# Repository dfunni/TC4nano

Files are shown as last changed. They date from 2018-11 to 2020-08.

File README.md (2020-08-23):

# TC4nano
The TC4nano is an Arduino Nano shield for termperature logging (up to 4 thermocouples) and PID control of a resistive heating element for use in home coffee roasting (based off of the TC4 Arduino Uno shield design copyright 2014 MLG Properties LLC and bvwelch.com CC-BY). The TC4nano includes one onboard SSR for heater control via slow PWM. Forced air is recommended for cooling the SSR in configurations drawing 10A or above.

### CONTENTS:
1. Configuring Artiasn
2. Updating TC4 Firmware
3. Troubleshooting

The TC4nano is pre-configured for the Artisan roaster-scope software using the aArtisanQ_PID_6_2_3 by Jim Gallt and Brad
Collins provided under BSD Liscense.

TC4 firmware can be found at:
https://github.com/greencardigan/TC4-shield

Artisan can be found at:	
https://github.com/artisan-roaster-scope

Artisan installation instructions:
https://github.com/artisan-roaster-scope/artisan/blob/master/wiki/Installation.md

## 1. CONFIGURING ARTISAN

### General Config
The configuration below assumes use with Poppery I roaster and no fan control through Artisan. 

For Poppery II or other DC fan systems, fan control can be added by connecting a DC motor driver to the IO3 jumper. For AC fan control, zero cross detection circuitry and an additional random fire SSR are required as well as reflashing the Arduino firmware with different configuration settings. For Artisan configuration with fan control see the setup described here: https://www.youtube.com/watch?v=0-Co-pXF2NM. 

#### Config > Device...

ET/BT tab:
- select TC4 radio button
- ET Channel - 2
- BT Channel - 1
- AT Channel - None
- PID Firmware - unchecked
- Control - checked
- Curves: ET - unchecked BT - checked
- LCDs: ET - unchecked BT - checked Swap - unchecked

Extra Devices tab:
- Add two devices

Device 1: 
- Device - ArduinoTC4 56 
- Label1 - "Heater" 

Device 2:
- Device - ArduinoTC4 78
- Label1 - "SV" 
- Label2 - "AT"

Note: after clicking "OK" in the Device menu the Port menu will automatically pop up. Prior to each roast session ensure the port reflects the correct Arduino.

#### Config > Sampling Interval 
- set to "1.0" seconds

#### Config > Curves... > RoR tab
- check the boxes for curves and LCDs you want to view and check projection

#### Config > Events

Config tab:
- Annotations - check
- 1 - uncheck - Fan
- 2 - check - Heater
- 3 - uncheck - Damper
- 4 - uncheck - Burner
- Auto CHARGE/Auto Drop/Mark MET/Show Time Guide - uncheck

Buttons tab:
- add one button
- Label - "Heater Off"
- Type - Heater
- Value - 0
- Action - Serial Command
- Documentation - "OT1;0"
- Visibility - ON

Sliders tab:
- In the heater row set the following to:
- Heater - check
- Action - Serial Command
- Command - "OT1;{}"
- Offset - 0.0
- Factor - 1
- Min - 0
- Max - 100
- Fan - uncheck
- Damper - uncheck
- Burner - uncheck

#### Config > Temperature
- Select Fahrenheit or Celcius mode

### PID Config

Click the blue CONTROL button (ensure Control is checked under Config > Device)

Recommended starting PID parameters:

| | kp  | ki | kd  |
|---|-----|---|-----|
| Poppery I  | 2.2 | 0.08 | 20  |
| Poppery II | 1.3 | 0.06 | 4.5 |

- Source - BT

Target:
- Positive - Heater
- Negative - None

Set Value:
- Mode - Background (ensure background profile is loaded prior to roasting)
- Lookahead - 10s (adjust as necessary)

- Start PID on CHARGE - check

### Creating a Profile

#### Tools > Designer

Adjust the circles to the desired locations, add or delete points as necessary.

When profile is complete go to Tools > Designer (uncheck) and proile will be
loaded onto the graph.

Hit the RESET button, then save the profile to your Profiles directory.

### Loading a Background Profile

#### Roast > Background

- Show - check
- BT - check
- All others - uncheck
- Align - CHARGE
- Load - select a saved profile from your profile directory

## 2. UPDATING TC4 FIRMWARE

The latest version of the TC4 firmware can be found on github. Version 
6.6 zip file can be found at:
https://github.com/greencardigan/TC4-shield/tree/master/applications/Artisan/aArtisan_PID/tags/REL_aArtisanQ_PID_6_6

Once downloaded open aArtisanQ_PID.ino in the Arduino IDE 
(https://www.arduino.cc). This will open all of the other files from the
aArtisanQ_PID folder as seperate tabs in the IDE.

Select the user.h tab and to choose the options you wish to enable by 
uncommenting/commenting the options in this file.

- Under "Base configuration" ensure CONFIG_PWM is selected as the 
TC4nano does not include a ZCD.

- Under "Tempreature Unit" comment out CELCIUS if Fahrenhiet is desired.

When all appropriate changes are made, connect the Arduino to the computer and
select the following settings from the menu bar:

- Tools > Board > Arduino Nano
- Tools > Processor > ATMega328P (Old Bootloader)
- Tools > Port > /dev/cu.YOUR_ARDUINO

Finally, flash the Adduino Nano by clicking the upload (forward arrow) button 
in the Arduino IDE. A display of the progress will appear in the command prompt
at the bottom of the IDE and "Done Uploading" will display when it completes 
sucessfully.

## 3. TROUBLESHOOTING:

### Generic Arduino Not Recognized (macOS)

Copy and paste these commands into terminal one by one 
(to open terminal press command+space and type 'terminal', then hit enter):

First check to see if homebrew is installed

    brew --version

If it is not installed (ie you get an output that is something other than
the version of homebrew) run the following commmand

    /usr/bin/ruby -e "$(curl -fsSL https://raw.githubusercontent.com/Homebrew/install/master/install)"

Then run the following two commands to install the CH34x drivers needed
to use the generic arduino nano

    brew tap mengbo/ch340g-ch34g-ch34x-mac-os-x-driver https://github.com/mengbo/ch340g-ch34g-ch34x-mac-os-x-driver
    brew cask install wch-ch34x-usb-serial-driver

Now restart your computer, and see if Artisan recognizes the arduino.
Alternately, you can enter the following in the terminal and look for an output
that is not an error.

    ls /dev/cu.usb* /dev/cu.wch*

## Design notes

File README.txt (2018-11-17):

# TC4nano
The configuration specified in this document is for the TC4nano which uses
one SSR for heater control (no fan control) and logs BT only.

CONTENTS:
Configuring Artiasn
- General Config
- PID Config
- Creating a Profile
- Loading a Background Profile
Updating TC4 Firmware
Troubleshooting
- Generic Arduino Nano Not Recognized

The TC4nano is configured for the Artisan roaster-scope software. The latest 
version can be found at:	
https://artisan-roasterscope.blogspot.com

Artisan installation instructions:
https://github.com/artisan-roaster-scope/artisan/blob/master/wiki/Installation.md

The TC4nano comes preloaded with aArtisanQ_PID_6_2_3 by Jim Gallt and Brad
Collins and is provided under BSD Liscense. 

The provided firmware has been tested with Artisan versions up to 1.5. 
If you wish to update the firmware the instructions are provided below.

*******************************************************************************

CONFIGURING ARTISAN

Leave defaults unless specified below. Text input is listed in " ".

===============================================================================
General Config
---------------------------------
Config > Device...

> ET/BT tab:
select TC4 radio button
ET Channel - 1
BT Channel - 2
AT Channel - None
PID Firmware - unchecked
Control - checked
Curves: ET - unchecked BT - checked
LCDs: ET - unchecked BT - checked Swap - unchecked

> Extra Devices tab:
Add two devices

Device 1: 
Device - ArduinoTC4 56 
Label1 - "Heater" 
Label2 - "Fan"

Device 2:
Device - ArduinoTC4 78
Label1 - "SV" 
Label2 - "AT"
OK

Note: after clicking "OK" in the Device menu the Port menu will automatically
pop up. Leave this as default for now. When roasting ensure the port reflects
the TC4's Arduino.
OK
---------------------------------

Config > Sampling Interval 
set to "1.0" seconds
OK
---------------------------------

Config > Curves... > RoR tab
check the boxes for curves and LCDs you want to view and check projection
OK
---------------------------------

Config > Events

> Config tab:
Annotations - check
1 - check - "Fan"
2 - check - "Heater"
3 - uncheck
4 - uncheck
Auto CHARGE/Auto Drop/Mark MET/Show Time Guide - uncheck

> Buttons tab
add one button
Label - "Fan Off"
Type - Fan
Value - 0
Action - Serial Command
Documentation - "IO3;0"
Visibility - ON

> Sliders tab
In the heater row set the following to:
Heater - check
Action - Serial Command
Command - "OT1;{}"
Offset - 0.0
Factor - 1
Min - 0
Max - 100

Fan - uncheck
Damper - uncheck
Burner - uncheck
OK
---------------------------------
Config > Temperature
Select Fahrenheit or Celcius mode
OK
---------------------------------

===============================================================================
PID Config

Click the blue CONTROL button (ensure Control is checked under Config > Device)

For Poppery I a good starting point is:
kp = 2.2; ki = 0.08; kd = 20

For Poppery II start with:
kp = 1.3; ki = 0.06; kd = 4.5

Source - BT

Target:
Positive - Heater
Negative - None

Set Value:
Mode - Background (ensure background profile is loaded prior to roasting)
Lookahead - 10s (adjust as necessary)

Start PID on CHARGE - check
OK

===============================================================================
Creating a Profile

Tools > Designer

Adjust the circles to the desired locations, add or delete points as necessary.

When profile is coplete go to Tools > Designer (uncheck) and proile will be
loaded onto the graph.

Hit the RESET button, then save the profile to your Profiles directory.

===============================================================================
Loading a Background Profile

Roast > Background

Show - check
BT - check
All others - uncheck
Align - CHARGE
Load - select a saved profile from your profile directory
OK

*******************************************************************************

UPDATING TC4 FIRMWARE

The latest version of the TC4 firmware can be found on github. Version 
6.6 zip file can be found at:
https://github.com/greencardigan/TC4-shield/tree/master/applications/Artisan/aArtisan_PID/tags/REL_aArtisanQ_PID_6_6

Once downloaded open aArtisanQ_PID.ino in the Arduino IDE 
(https://www.arduino.cc). This will open all of the other files from the
aArtisanQ_PID folder as seperate tabs in the IDE.

Select the user.h tab and to choose the options you wish to enable by 
uncommenting/commenting the options in this file.

- Under "Base configuration" ensure CONFIG_PWM is selected since the 
TC4nano does not include a ZCD.

- Under "Tempreature Unit" comment out CELCIUS if Fahrenhiet is desired.

- Leave all 4 "TC_TYPEx typeK" enabled under "Thermocouple Input Options"
even though only one thermocouple will be used.

- Ensure Baud rate of BAUD 115200

When all appropriate changes are made, connect the arduino to the computer and
select the following options from the menu bar:

Tools > Board > Arduino Nano
Tools > Processor > ATMega328P (Old Bootloader)
Tools > Port > /dev/cu.YOUR_ARDUINO

Finally, flash the Adduino Nano by clicking the upload (forward arrow) button 
in the Arduino IDE. A display of the progress will appear in the command prompt
at the bottom of the IDE and "Done Uploading" will display when it completes 
sucessfully.

*******************************************************************************

TROUBLESHOOTING:

===============================================================================
Generic Arduino Not Recognized

Copy and paste these commands into terminal one by one 
(to open terminal press command+space and type terminal, then hit enter):

First check to see if homebrew is installed

_______________________________________________________________________________
brew -v
_______________________________________________________________________________

If it is not installed (ie you get an output that is something other than
the version of homebrew) run the following commmand... this takes a while

_______________________________________________________________________________
/usr/bin/ruby -e "$(curl -fsSL https://raw.githubusercontent.com/Homebrew/install/master/install)"
_______________________________________________________________________________

Then run the following two commands to install the CH34x drivers needed
to use the generic arduino nano

_______________________________________________________________________________
brew tap mengbo/ch340g-ch34g-ch34x-mac-os-x-driver https://github.com/mengbo/ch340g-ch34g-ch34x-mac-os-x-driver
_______________________________________________________________________________

_______________________________________________________________________________
brew cask install wch-ch34x-usb-serial-driver
_______________________________________________________________________________

Now restart your computer, and see if Artisan recognizes the arduino.
Or you can enter the following in the terminal and look for an output
that is not an error.

_______________________________________________________________________________
ls /dev/cu.usb* /dev/cu.wch*
_______________________________________________________________________________

===============================================================================

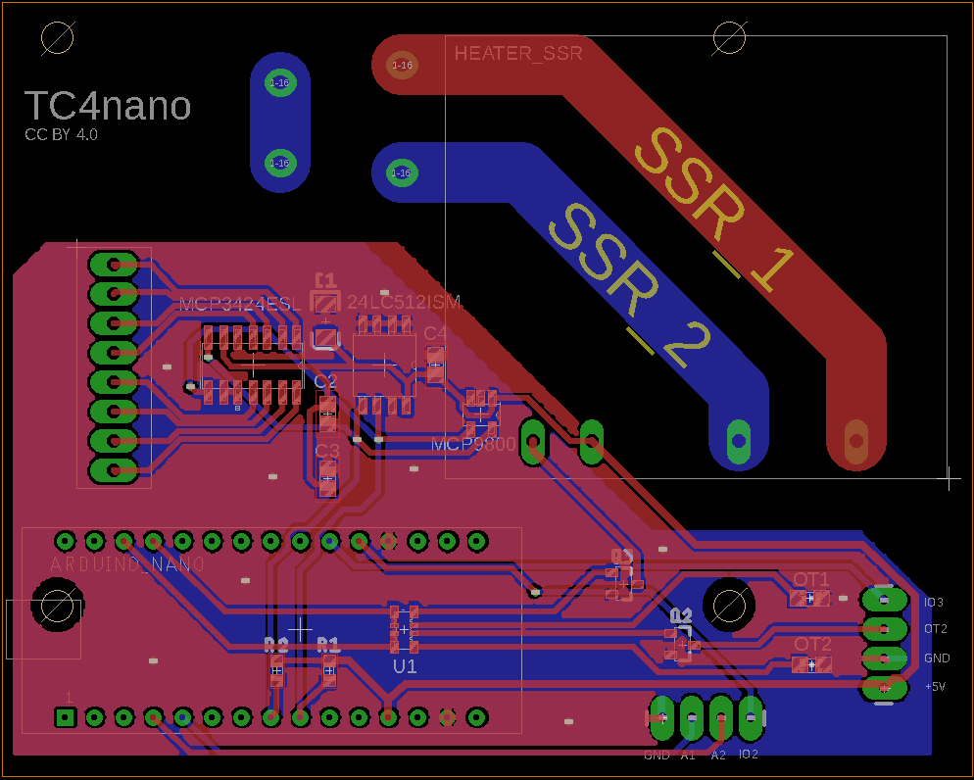
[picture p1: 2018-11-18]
Hardware/TC4nano_v2_brd.png

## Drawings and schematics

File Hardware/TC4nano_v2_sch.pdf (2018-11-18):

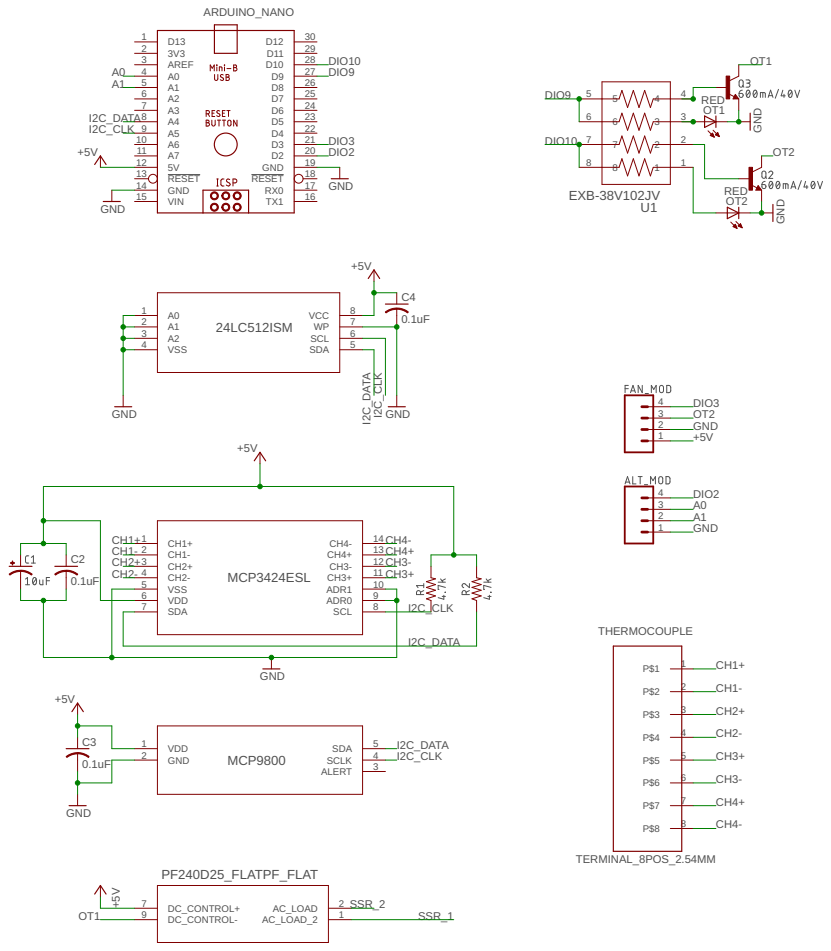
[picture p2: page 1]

2 | 7 VCC
3 | 6 WP

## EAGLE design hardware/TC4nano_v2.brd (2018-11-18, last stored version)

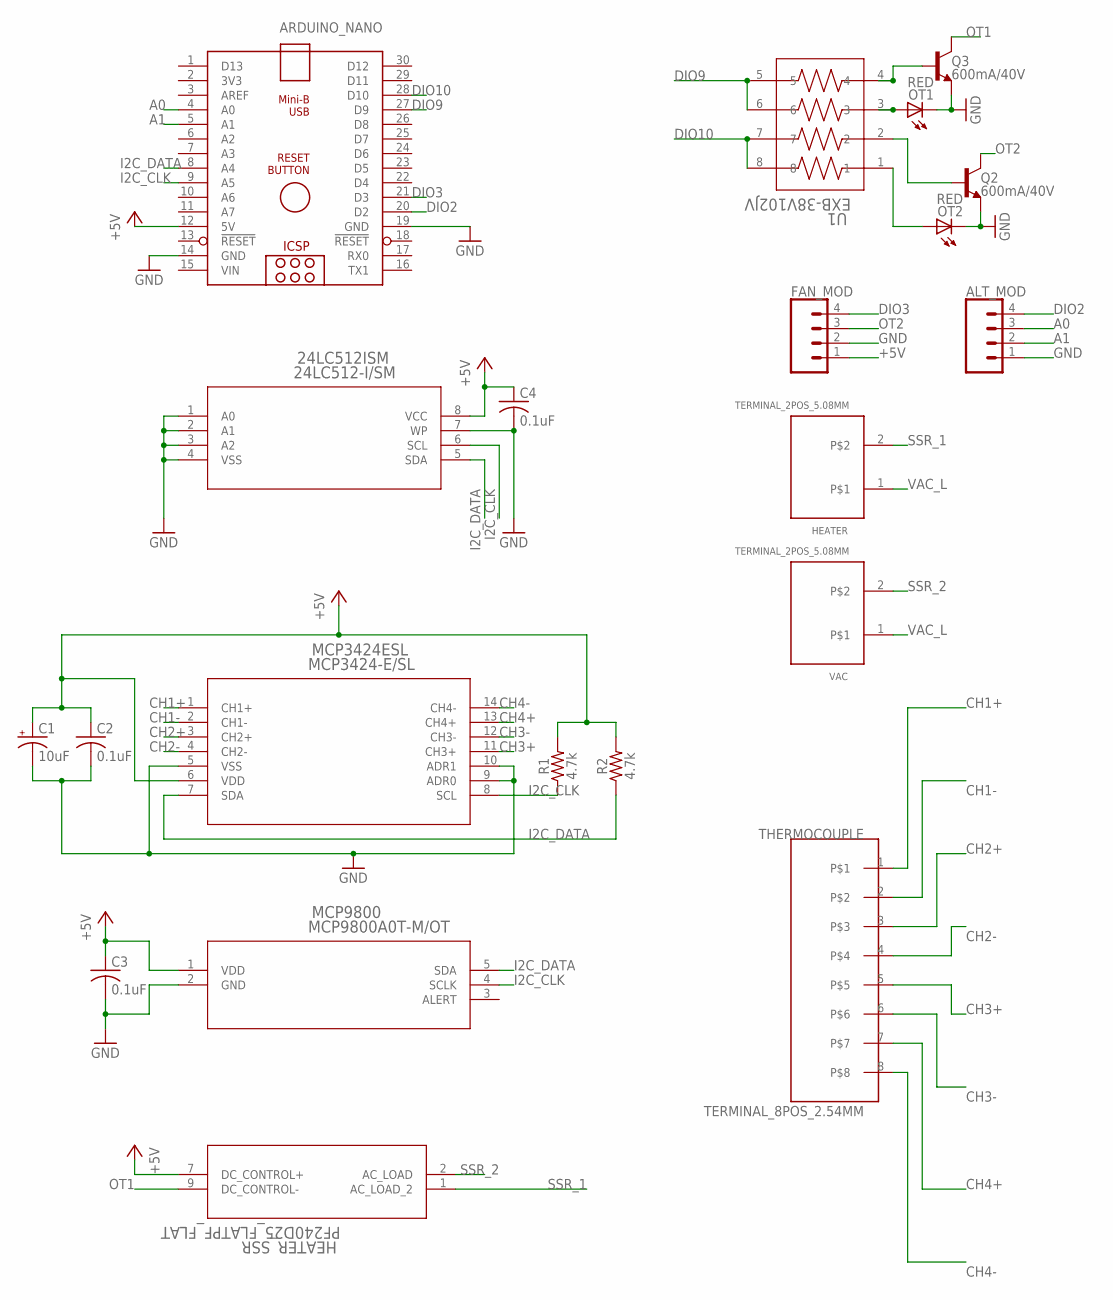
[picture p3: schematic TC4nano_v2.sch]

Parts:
24LC512ISM: 24LC512-I/SM; SOIC8-W_MC
ALT_MOD: CONN_04LONGPADS; 1X04_LONGPADS
ARDUINO_NANO: ARDUINO_NANO
C1: 10uF; EIA3216
C2, C3, C4: 0.1uF; C0805
FAN_MOD: CONN_04LONGPADS; 1X04_LONGPADS
HEATER: TERMINAL_2POS_5.08MM
HEATER_SSR: PF240D25_FLATPF_FLAT; RELAY_PF_FLAT
MCP3424ESL: MCP3424-E/SL; SOIC14-N_MC
MCP9800: MCP9800A0T-M/OT; SOT-23-5_MC
OT1, OT2: RED; CHIPLED_0805
Q2, Q3: 600mA/40V; SOT23-3
R1, R2: 4.7k; 0603
THERMOCOUPLE: TERMINAL_8POS_2.54MM
U1: EXB-38V102JV; C_ARRAY_EXB38V
VAC: TERMINAL_2POS_5.08MM

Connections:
+5V: 24LC512ISM.8 (VCC), ARDUINO_NANO.12 (5V), C1.+, C2.1, C3.1, C4.1, FAN_MOD.1, HEATER_SSR.7 (DC_CONTROL+), MCP3424ESL.6 (VDD), MCP9800.1 (VDD), R1.2, R2.2
A0: ALT_MOD.3, ARDUINO_NANO.4 (A0)
A1: ALT_MOD.2, ARDUINO_NANO.5 (A1)
CH1+: MCP3424ESL.1 (CH1+), THERMOCOUPLE.1
CH1-: MCP3424ESL.2 (CH1-), THERMOCOUPLE.2
CH2+: MCP3424ESL.3 (CH2+), THERMOCOUPLE.3
CH2-: MCP3424ESL.4 (CH2-), THERMOCOUPLE.4
CH3+: MCP3424ESL.11 (CH3+), THERMOCOUPLE.5
CH3-: MCP3424ESL.12 (CH3-), THERMOCOUPLE.6
CH4+: MCP3424ESL.13 (CH4+), THERMOCOUPLE.7
CH4-: MCP3424ESL.14 (CH4-), THERMOCOUPLE.8
DIO2: ALT_MOD.4, ARDUINO_NANO.20 (D2)
DIO3: ARDUINO_NANO.21 (D3), FAN_MOD.4
DIO9: ARDUINO_NANO.27 (D9), U1.5, U1.6
DIO10: ARDUINO_NANO.28 (D10), U1.7, U1.8
GND: 24LC512ISM.1 (A0), 24LC512ISM.2 (A1), 24LC512ISM.3 (A2), 24LC512ISM.4 (VSS), 24LC512ISM.7 (WP), ALT_MOD.1, ARDUINO_NANO.14 (GND), ARDUINO_NANO.19 (GND), C1.-, C2.2, C3.2, C4.2, FAN_MOD.2, MCP3424ESL.5 (VSS), MCP3424ESL.9 (ADR0), MCP3424ESL.10 (ADR1), MCP9800.2 (GND), OT1.C, OT2.C, Q2.2 (E), Q3.2 (E)
I2C_CLK: 24LC512ISM.6 (SCL), ARDUINO_NANO.9 (A5), MCP3424ESL.8 (SCL), MCP9800.4 (SCLK), R1.1
I2C_DATA: 24LC512ISM.5 (SDA), ARDUINO_NANO.8 (A4), MCP3424ESL.7 (SDA), MCP9800.5 (SDA), R2.1
unnamed: Q2.1 (B), U1.2
unnamed: OT2.A, U1.1
unnamed: Q3.1 (B), U1.4
unnamed: OT1.A, U1.3
OT1: HEATER_SSR.9 (DC_CONTROL-), Q3.3 (C)
OT2: FAN_MOD.3, Q2.3 (C)
SSR_1: HEATER.2, HEATER_SSR.1 (AC_LOAD_2)
SSR_2: HEATER_SSR.2 (AC_LOAD), VAC.2
VAC_L: HEATER.1, VAC.1
VIN: ARDUINO_NANO.15 (VIN)

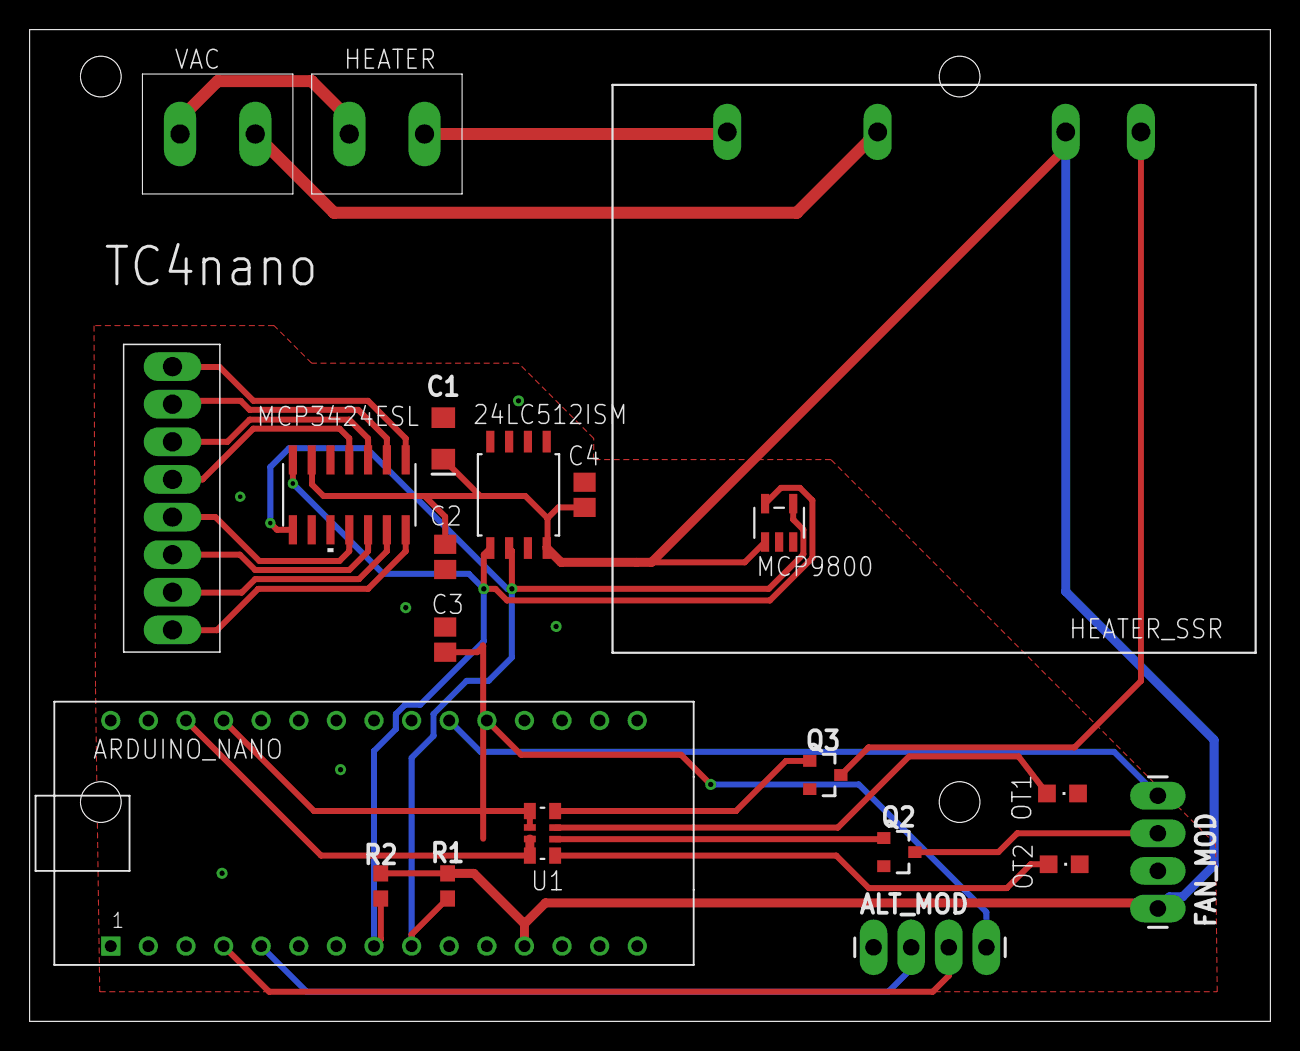
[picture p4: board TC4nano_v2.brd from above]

Board: 2 copper layers, 83.8 x 67.0 mm, 21 parts (0 on the bottom side), 27 nets.

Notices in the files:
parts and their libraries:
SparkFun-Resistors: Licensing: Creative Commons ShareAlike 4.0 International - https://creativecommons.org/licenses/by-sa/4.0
